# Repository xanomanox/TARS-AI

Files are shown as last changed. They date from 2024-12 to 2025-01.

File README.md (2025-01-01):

<h1 align="center">TARS-AI</h2>

<p align="center">
    <a href="https://discord.gg/uXkqkz3mJJ">
      
    </a>
    <a href="https://www.youtube.com/@TARS-AI.py.youtube">
        
    </a>
    <a href="https://www.instagram.com/tars.ai.py">
        
    </a>
    <a href="https://www.tiktok.com/@tars.ai.py">
        
    </a>
</p>

<p align="center"></p>

A recreation of the TARS robot from Interstellar, featuring AI capabilities and servo-driven movement. 

## Table of Contents
- [Hardware Requirements](#hardware-requirements)
- [Software Stack](#software-stack)
- [Build Modifications](#build-modifications)
- [License](#license)
- [Contributing](#contributing)
- [Additional Resources](#additional-resources)

## Hardware Requirements 

Everything here is **under development** and is subject to change.

| Category | Component | Description | Link |
|---|---|---|---|
| **Printing** | Bambu Labs Printer | Compatible models: P1S, A1, X1C | - |
| | TPU Filament (Bambu) | For all "Flexor" parts | [Buy](https://us.store.bambulab.com/products/tpu-for-ams) |
| | TPU Filament (Alternative) | Overture TPU filament | [Buy](https://www.amazon.com/Overture-Filament-Flexible-Consumables-Dimensional/dp/B07VDP2S3P/) |
| | PETG Filament | For all non-Flexor parts | [Buy](https://us.store.bambulab.com/products/petg-hf) |
| | PLA Filament | Optional - for rapid prototyping | - |
| **Core Components** | Raspberry Pi 5 | Main computing unit | [Buy](https://www.amazon.com/Raspberry-Pi-Quad-core-Cortex-A76-Processor/dp/B0CTQ3BQLS/) |
| | 3.5" LCD Display | Interface display | [Buy](https://www.amazon.com/OSOYOO-3-5inch-Display-Protective-Raspberry/dp/B09CD9W6NQ/) |
| | 16-Channel PWM Servo Driver | I2C Interface | [Buy](https://www.amazon.com/gp/product/B00EIB0U7A/) |
| | Buck Converter | Power management | [Buy](https://www.amazon.com/gp/product/B07SGJSLDL/) |
| **Servo Motors** | diymore MG996R | Digital servo motors (2x 90g micro servos per leg) | [Buy](https://www.amazon.com/diymore-6-Pack-MG996R-Digital-Helicopter/dp/B0CGRP59HJ/) |
| | MG996R 55g (Alternative) | Digital RC servo motors with high torque | - |
| **Drive Train** | Bearings | Motion support | [Buy](https://www.amazon.com/gp/product/B07FW26HD4/) |
| | Springs | Motion dampening | [Buy](https://www.amazon.com/gp/product/B076M6SFFP/) |
| | Metal Rods (Option 1) | Structural support | [Buy](https://www.amazon.com/gp/product/B01MAYQ12S/) |
| | Metal Rods (Option 2) | Alternative structural support | [Buy](https://www.amazon.com/gp/product/B0CTSX8SJS/) |
| | Linkage | Motion transfer | [Buy](https://www.amazon.com/gp/product/B0CRDRWYXW/) |
| | Servo Extension Wires | Connection cables | [Buy](https://www.amazon.com/OliYin-7-87in-Quadcopter-Extension-Futaba/dp/B0711TBZY2/) |
| **Audio System** | Raspberry Pi Microphone | Audio input | [Buy](https://www.amazon.com/gp/product/B086DRRP79/) |
| | Audio Amplifier | Sound processing | [Buy](https://www.amazon.com/dp/B0BTBS5NW2) |
| | Speaker | Audio output | [Buy](https://www.amazon.com/dp/B07GJ4GH67) |
| **Camera System** | Camera Module | Visual input | [Buy](https://a.co/d/50BbE8a) |
| | Camera Ribbon Cable | Camera connection | [Buy](https://www.amazon.com/Onyehn-Raspberry-Camera-Cable-Ribbon/dp/B07XZ5DX5H/) |
| **Fasteners** | M3 20mm Screws | Mounting (6x needed) | [Buy](https://www.amazon.com/gp/product/B0CR6DY4SS/) |
| | M3 14mm Screws | Mounting (40x needed) | [Buy](https://www.amazon.com/gp/product/B0D9GW9K4G/) |
| | M3 10mm Screws | Mounting (76x needed) | [Buy](https://www.amazon.com/gp/product/B0CR6G5XWC/) |
| | M3 Asstd Grub Screws | Mounting (6-8 needed) | [Buy](https://www.amazon.com/dp/B07N7C6HKP/) |

## Software Stack

See [`ENVSETUP.md`](./ENVSETUP.md) for instructions on setting up the software environment.

GPTARS Software Demo (https://www.youtube.com/watch?v=4YObs8BV3Mc)

- **LLM**: Choice of:
  - OpenAI (Recommended)
  - Oobabooga
  - Tabby ([tabbyAPI](https://github.com/theroyallab/tabbyAPI))
  - Ollama (Soon)
- **Text-to-Speech**: Choice of:
  - Azure TTS
  - Local (E-speak)
  - Local (Piper TTS with custom Voice model) (Recommended)
  - XTTSv2 with voice cloning ([xtts-api-server](https://github.com/daswer123/xtts-api-server))
- **Speech-to-Text**:
  - Vosk
  - Whisper
- **Vision Handling**:
  - Saleforce Blip
- **Tool Utilization**:
  - Custom Module Engine

## Build Modifications
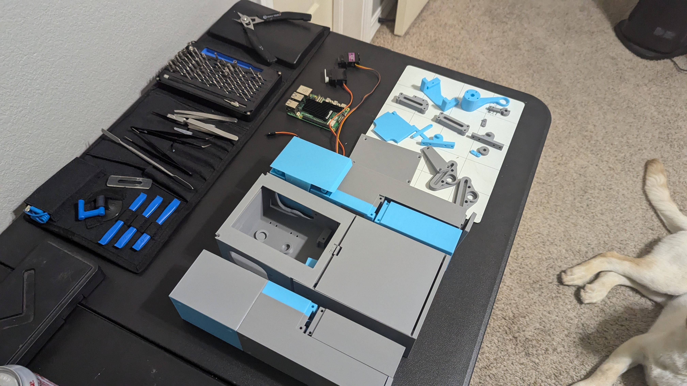
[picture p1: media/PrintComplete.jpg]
print

- Modified chassis bottom to accommodate SD card installation (See: "Chassis Bottom (Mod SD CARD).stl")

## License
[CC-BY-NU License](./LICENSE)

## Contributing
See [`CONTRIBUTING.md`](./CONTRIBUTING.md) for instructions on contributing to this project.

## Additional Resources
Inspirations + Credits to:
- [@charliediaz](https://www.hackster.io/charlesdiaz/how-to-build-your-own-replica-of-tars-from-interstellar-224833)
- [@gptars](https://www.youtube.com/@gptars)
- [@wizard.py](https://www.instagram.com/wizard.py/)
- [@poboisvert](https://github.com/poboisvert/GPTARS_Interstellar)

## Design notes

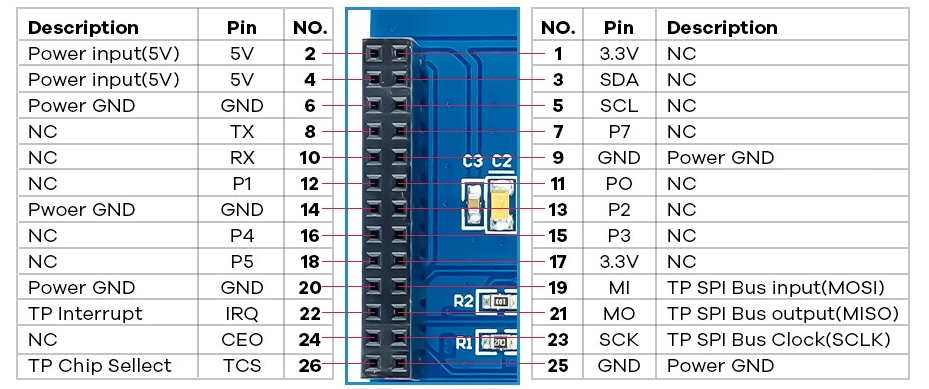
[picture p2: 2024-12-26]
Hardware/LCD PINOUT.png

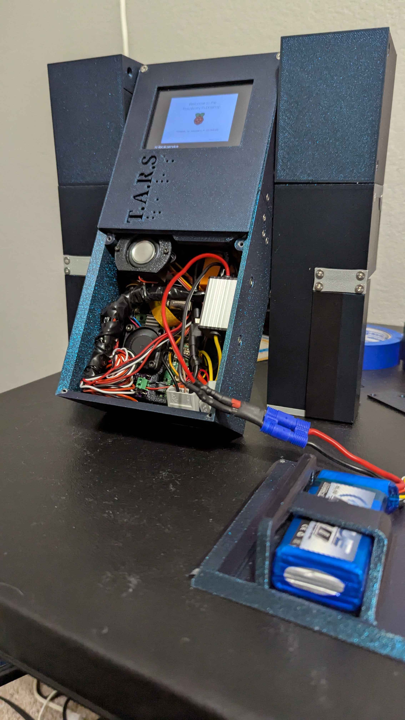
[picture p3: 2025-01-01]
media/preview.png

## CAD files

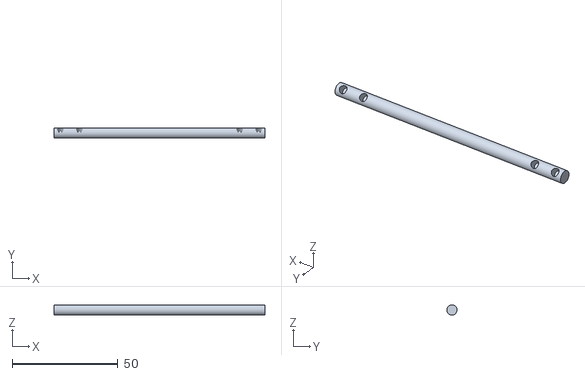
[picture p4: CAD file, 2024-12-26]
3d Printer Files/Main Axle.stl
100.0 x 4.80 x 4.80

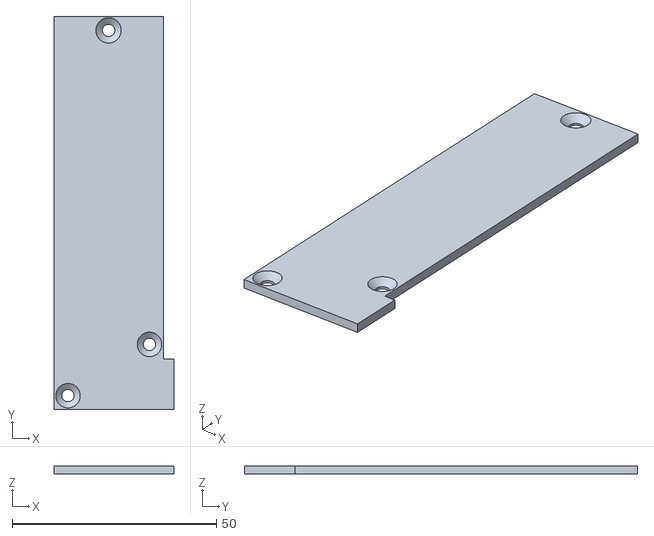
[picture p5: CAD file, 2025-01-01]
3d Printer Files/Arm Right Long Finger Lid countersunk.stl
29.4 x 96.3 x 2.00

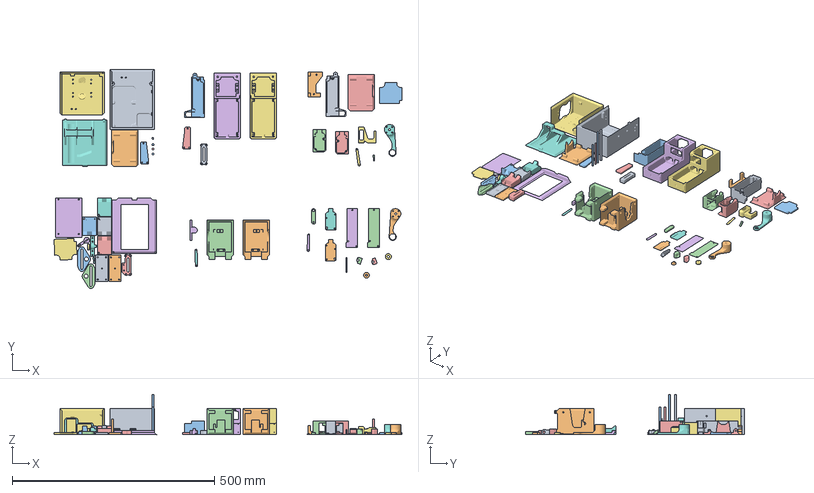
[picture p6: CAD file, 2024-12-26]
3d Printer Files/Other/GPTARs Files.3mf
859.8 x 541.4 x 100.0 mm
Main Axle.stl
Starboard Hull.stl
Lid B (1)(Mirror)(1).stl
Port Hull.stl
Port Component 233.stl
Starboard Suspension Mount.stl
Starboard Component 235.stl
Internal Hand 3 (1)(2)(2).stl
Main Arm (Mirror)_1.stl
Vertical Servo Clip (1).stl
Axle.stl
Forearm (1).stl
Forearm (1)(Mirror).stl
Port Component 234.stl
Screen Support.stl
Main Leg Mount (4).stl
Chassis (2).stl
Main Leg Mount (3).stl
Main ARM_1.stl
Lid Arm 2.stl
Servo Clip (Mirror).stl
Lid Arm 2(Mirror).stl
Chassis.stl
Lid Arm.stl
Sus Mount (1).stl
Lid Arm (Mirror).stl
Secondary Axle.stl
Pusher Rod.stl
Secondary Axle 2.stl
Internal Hand 3 (1)(2)(5).stl
TPU NewFlexor.stl
Lower Lid.stl
Conncting Arm.stl
Starboard Component 233.stl
Servi Clip.stl
Upper Strut Mount.stl
Upper Strut Mount 1.stl
Screen Lid.stl
Port NP - Mount Bearing.stl
Finger2.stl
Finger 2(Mirror).stl
Spacer.stl
Finger 1.stl
Internal Hand 1 (1)(2)(3).stl
Finger 1(Mirror).stl
Port Lid A.stl
Port Lid B.stl
Port Suspension Mount.stl
Foot Pad (1)(Mirror).stl
Port Foot Pad.stl
Starboard Spring Driver.stl
Port Spring Driver.stl
Sus Mount.stl
sk7_2 v1 (1).stl
Starboard NP - Mount Bearing.stl
Internal Hand 3 (1)(2).stl

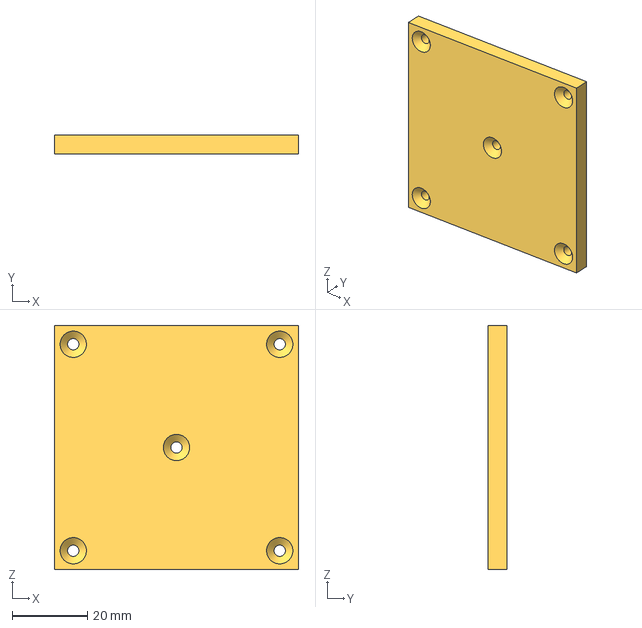
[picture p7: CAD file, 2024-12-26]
3d Printer Files/simplified_tars/footpad-simplified.3mf
65.0 x 5.00 x 65.0 mm

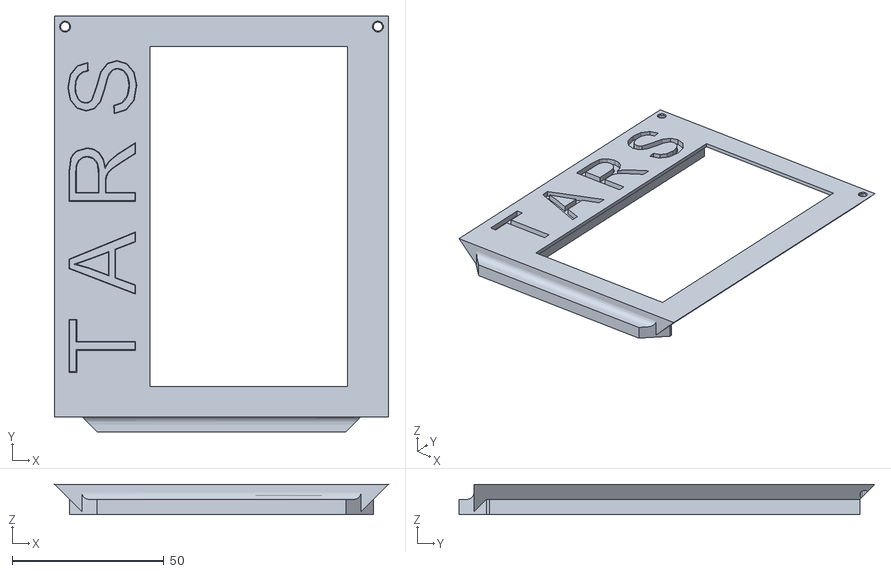
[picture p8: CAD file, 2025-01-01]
3d Printer Files/Chassis upper lid modded holes narrow 5in.stl
110.0 x 137.0 x 10.0

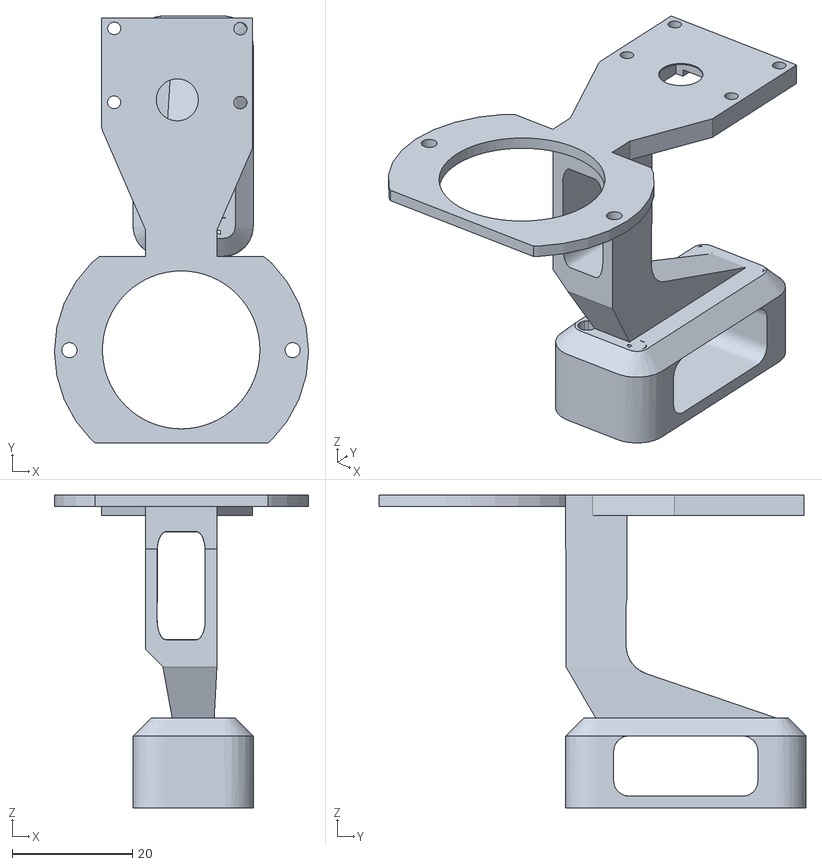
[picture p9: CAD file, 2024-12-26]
3d Printer Files/Other/RPI CAM and Speaker Mount.stl
42.3 x 71.1 x 52.1

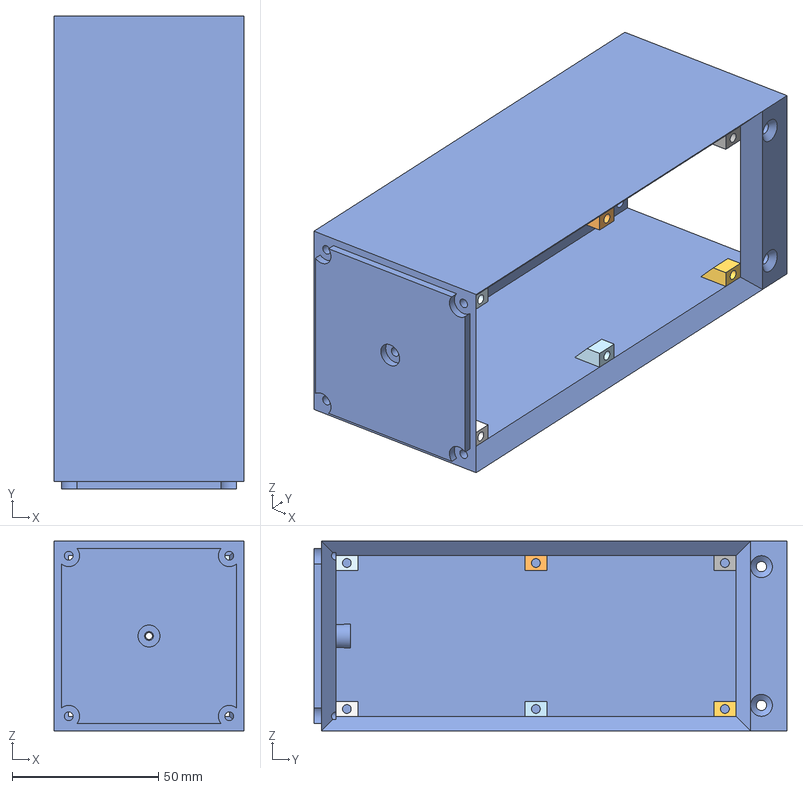
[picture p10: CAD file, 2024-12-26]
3d Printer Files/simplified_tars/leg - simplified.3mf
65.0 x 162.0 x 65.0 mm

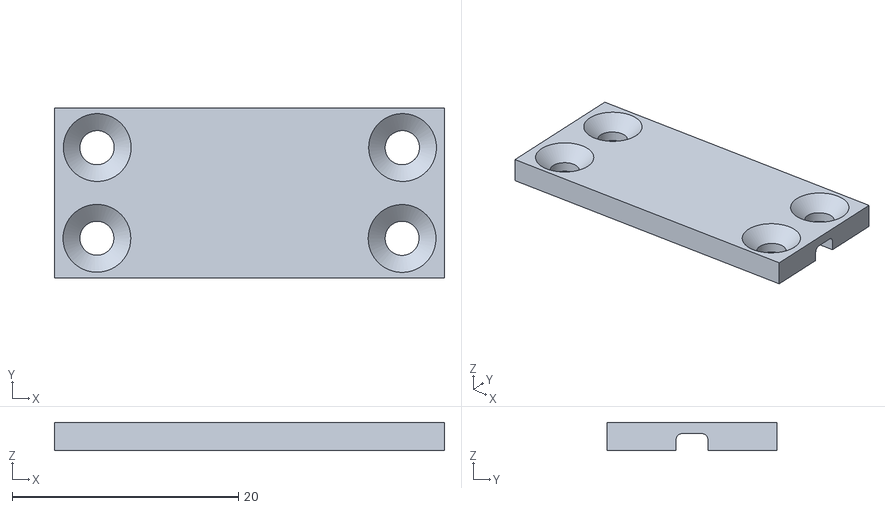
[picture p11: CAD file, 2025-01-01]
3d Printer Files/NewFlexor countersunk x2.stl
34.5 x 15.0 x 2.50

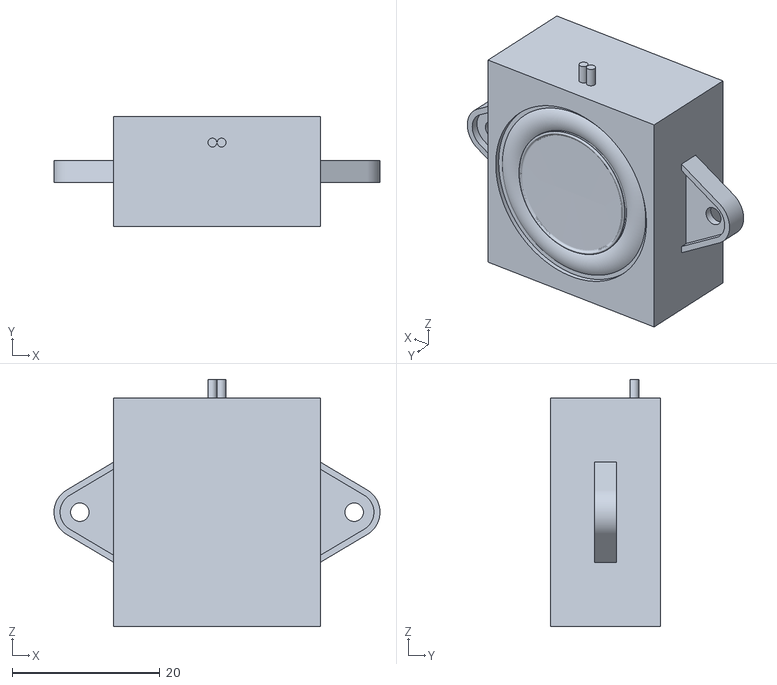
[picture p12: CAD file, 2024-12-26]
3d Printer Files/Other/Speaker.stl
44.2 x 14.9 x 33.5

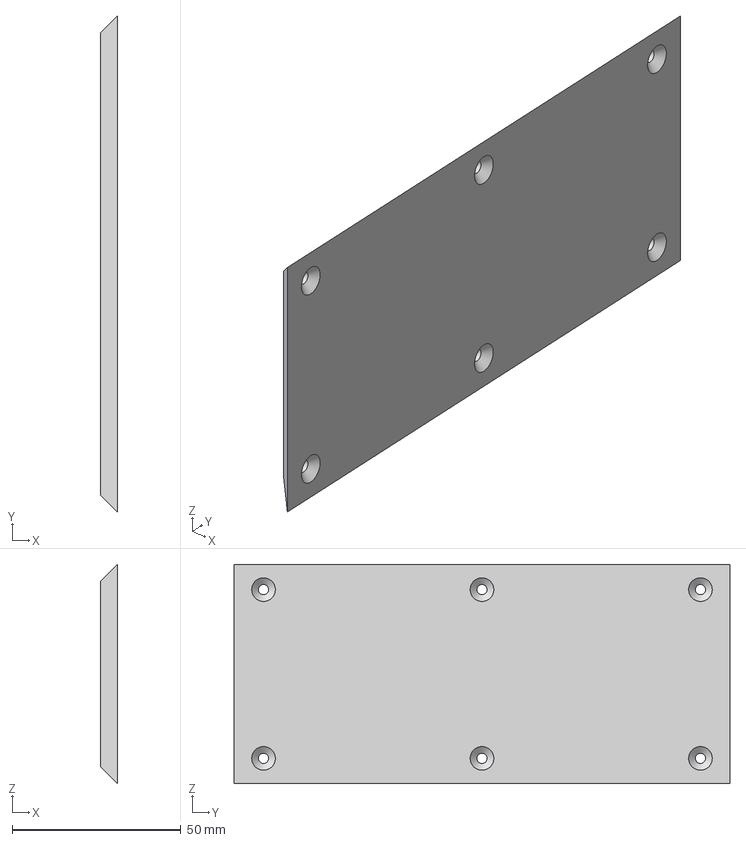
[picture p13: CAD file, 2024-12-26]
3d Printer Files/simplified_tars/leg_simplified-lid.3mf
5.00 x 147.0 x 65.0 mm

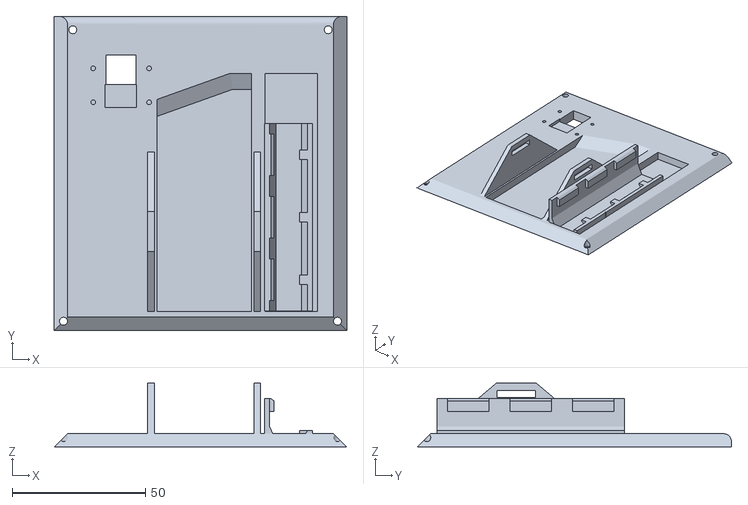
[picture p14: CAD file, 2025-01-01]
3d Printer Files/Chassis Lower Lid Pi camv3 and termblock (v9).stl
110.0 x 118.0 x 24.0

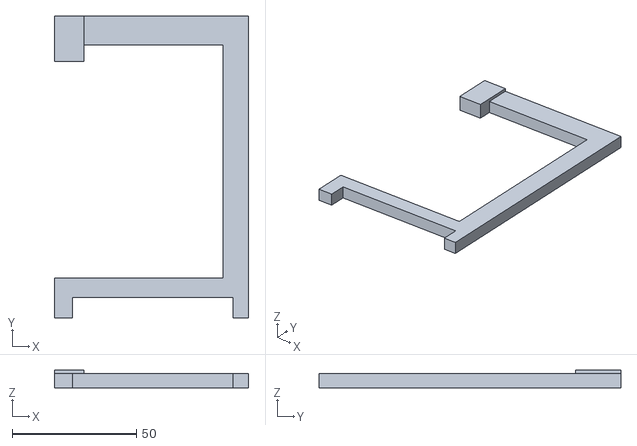
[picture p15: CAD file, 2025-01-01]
3d Printer Files/5in display spacer.stl
78.2 x 121.6 x 7.15

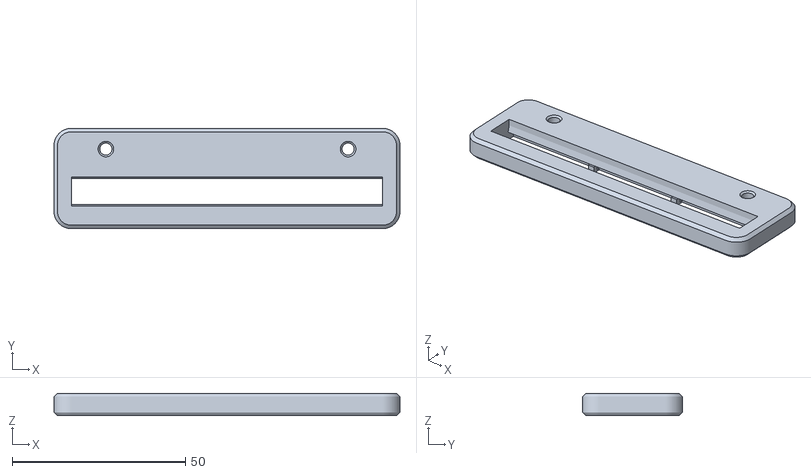
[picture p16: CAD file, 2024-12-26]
3d Printer Files/Other/PCT Linear Base Mount.stl
100.0 x 29.0 x 6.50

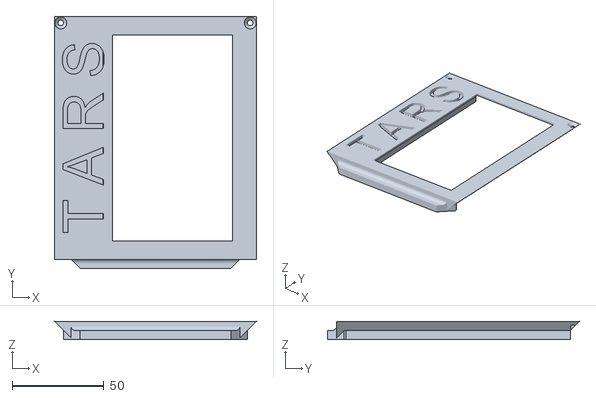
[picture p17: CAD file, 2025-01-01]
3d Printer Files/Chassis Upper Lid v9 5in narrow.stl
110.0 x 137.0 x 10.0

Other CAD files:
3d Printer Files/Chassis Lower Lid MOD PCT (mirror) makes space for GPIO.stl
3d Printer Files/Other/battery.stl
3d Printer Files/Chassis Upper Lid (v9) Speaker and Cam Mod.stl
3d Printer Files/Other/buck convertor.stl
3d Printer Files/Arm Chasis Lid x2.stl
3d Printer Files/Arm Left (Top Chassis).stl
3d Printer Files/Arm Left 1 Finger.stl
3d Printer Files/Arm Left 2 Finger.stl
3d Printer Files/Arm Left Footpad.stl
3d Printer Files/Arm Left Insert.stl
3d Printer Files/Arm Left Long Finger Lid.stl
3d Printer Files/Arm Left Long Finger.stl
3d Printer Files/Arm Left Lower Chasis.stl
3d Printer Files/Arm Left Lower Chassis MOD 3mm servoscrews.stl
3d Printer Files/Arm Left Mount.stl
3d Printer Files/Arm Left NP - Mount Bearing.stl
3d Printer Files/Arm Left Small Finger Lid.stl
3d Printer Files/Arm Left Spring Driver.stl
3d Printer Files/Arm Left Top Lid.stl
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

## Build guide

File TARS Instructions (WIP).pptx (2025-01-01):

## TARS Instructions

Screws Needed:
6 M20
40 M14
76 M10

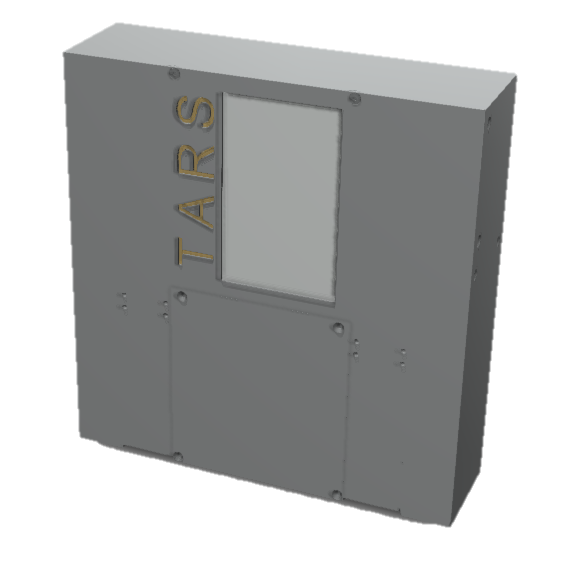
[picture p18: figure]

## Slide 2

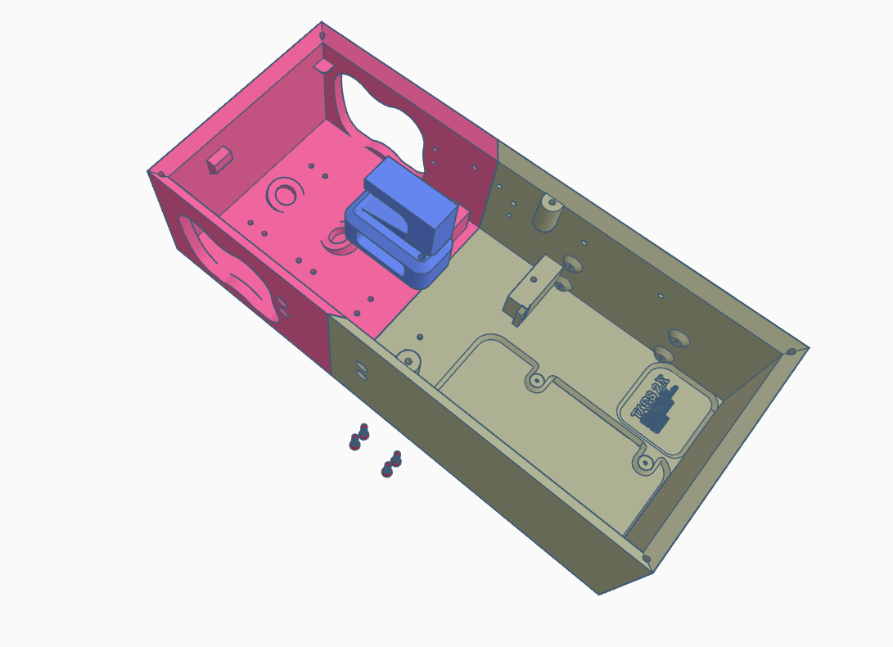
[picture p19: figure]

Chassis Upper (v9)

Chassis Lower (v9)

Chassis Connector Screen Support

M3 20MM x4

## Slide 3

x2

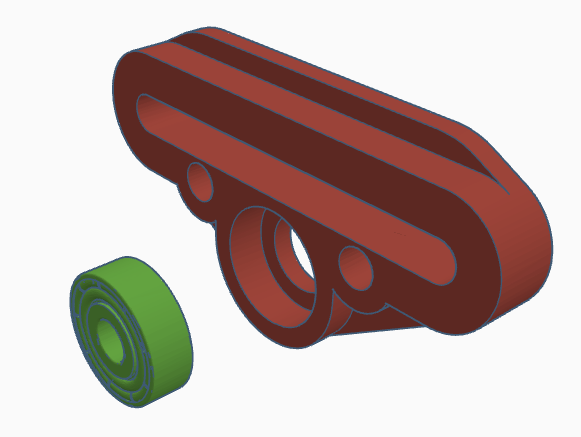
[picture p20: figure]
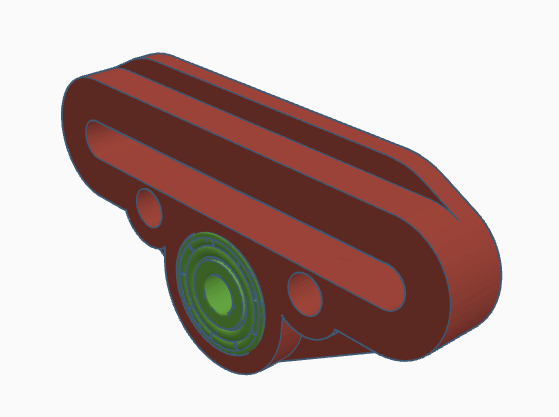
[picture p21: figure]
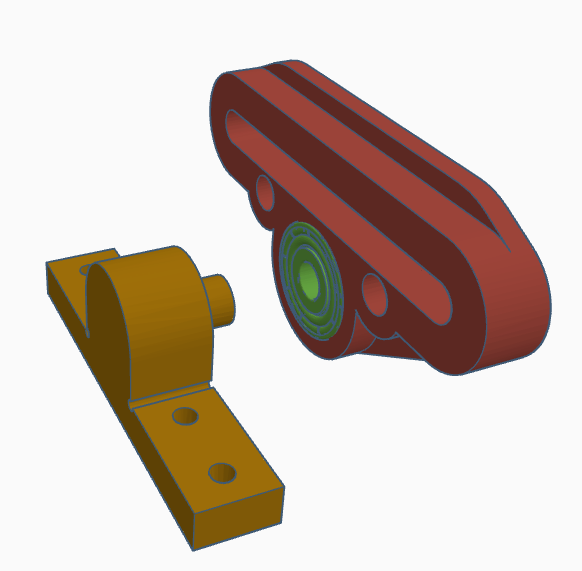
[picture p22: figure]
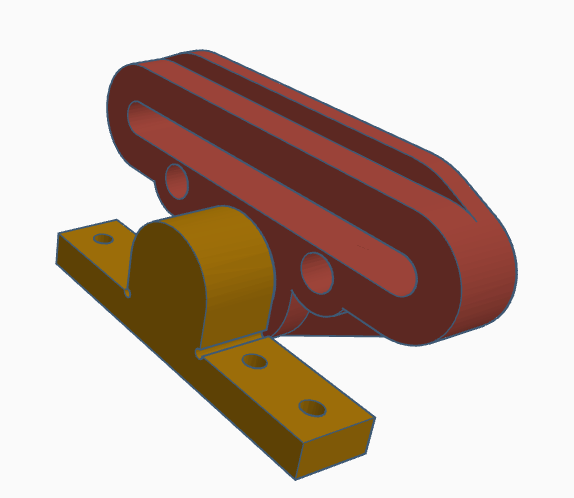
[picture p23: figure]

Arm Spring Divider
(left and Right)

608 Bearing
(metal or Printed)

Arm Suspension Mount

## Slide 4

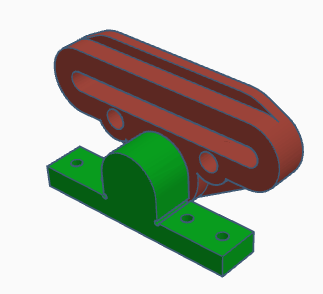
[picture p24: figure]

Assembly from previous step x2

Arm Suspension Mount x8

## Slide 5

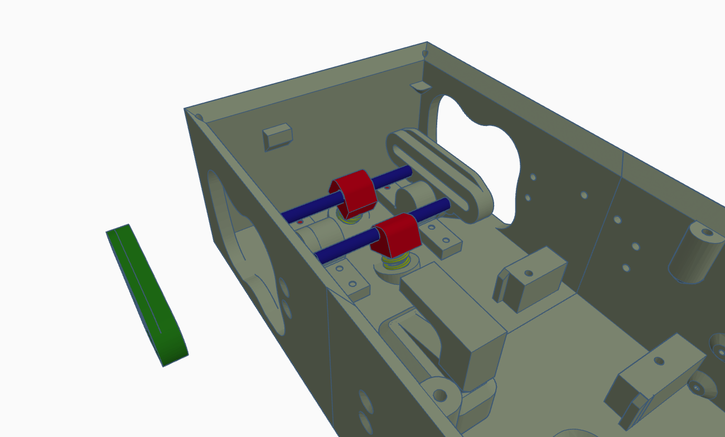
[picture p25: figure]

Secondary Axle x2

Spring x2

Upper Strut Mount x2

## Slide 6

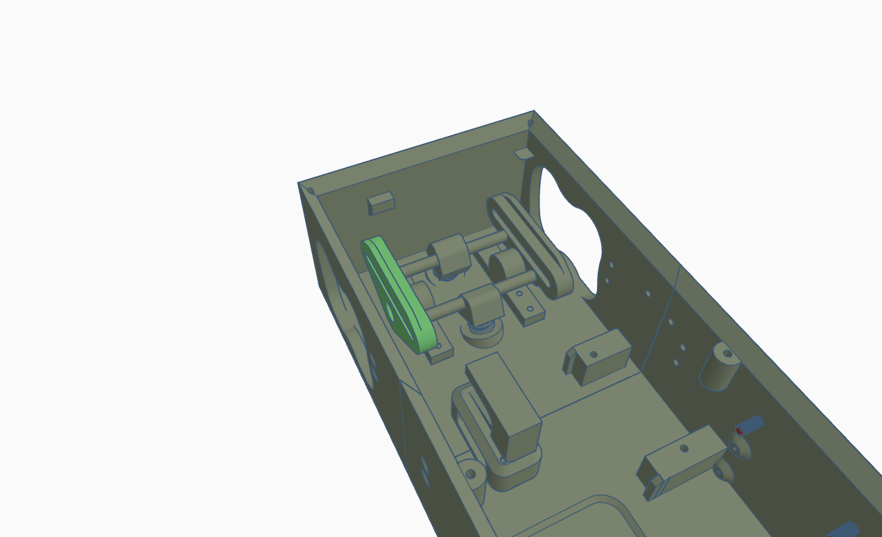
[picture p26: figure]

Reinstall

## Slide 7

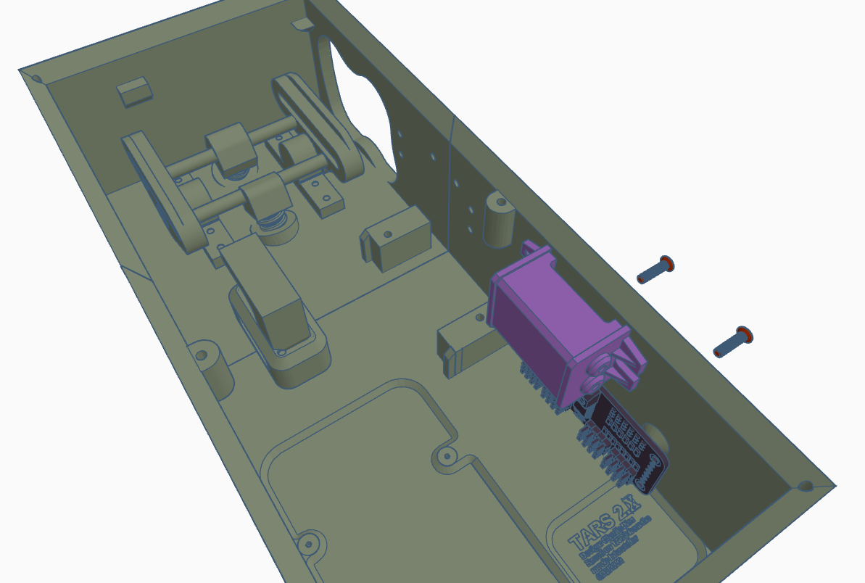
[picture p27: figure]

Secure the 12 ch PWM board to the wall with 4 M2*4 screws (use a flat tip by hand)
Connect the 6v out wires to the
Secure the 12v to 6v Buck convertor with 2 M3*10 screws

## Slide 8

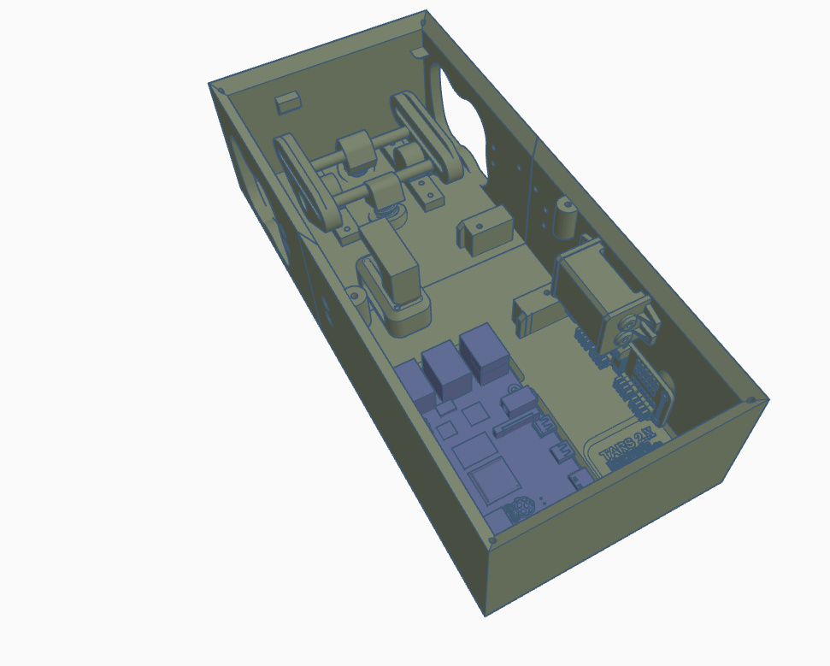
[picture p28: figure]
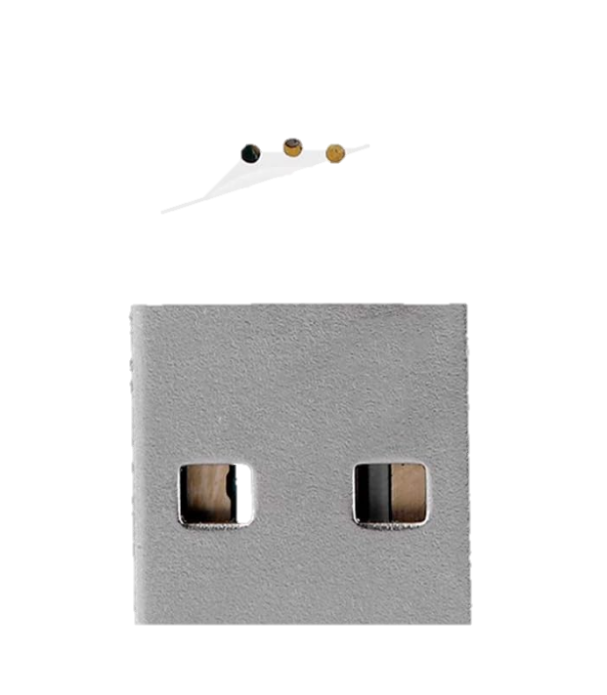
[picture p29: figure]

Insert the USB MIC into the RPI
(Not shown here)
Insert the RPI and secure with 4 M2*4 screws. DO NOT OVER TIGHTEN OR USE LONGER SCREWS

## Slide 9

“5 Pack ShareGoo 25T Aluminum Servo Horns M3 Threads Metal Steering Arm for RC Car Truck Buggy Airplane-Black”

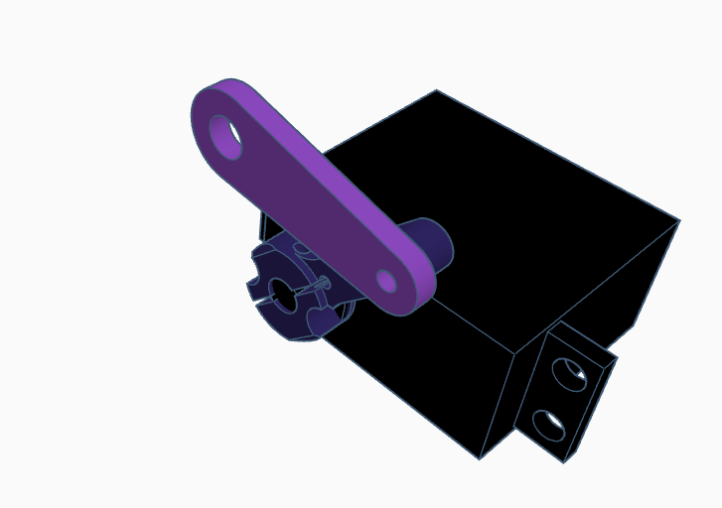
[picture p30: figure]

Attach a METAL !!! (unable to print it WILL strip) 25T Aluminum Servo Horn with M3 Threads to the servo using supplied hardware.
Attach upper connecting rod arm with M3*12 screw like arrow shown

## IMPORTANT STEP!!!!!!!

Connect Servos to the Servo Controller:
- Attach the center servo to the first set of pins on the servo controller (Pin 0).
- Connect the robot's left (port) arm to the next set of pins (Pin 1).
- Connect the robot's right (starboard) arm to the following set of pins (Pin 2).
Connect the PWM Servo Controller to the Raspberry Pi:
- Use the servotester.py script to determine the minimum and maximum PWM values the servo can operate within.
- Calculate the dead center value (midpoint) between the minimum and maximum PWM values.
- Manually attach the arms at the midpoint position to ensure proper alignment.
Update the Configuration File:
- Add the determined center PWM value as neutral to the config.ini file. Add 50 to neutral for up and subtract 50 for down limits.
Center the Arms Mechanically:
- Using the servo test tool, set each arm's servo channel to a midpoint value, such as 350 (between the typical range of 100-600).
- Detach the arms, reposition them to align mechanically with the center position, and then reattach them.
- This ensures the arms are mechanically centered at the specified midpoint value (e.g., 350). For example if you set 350 they should be vertical and perfectly straight.
Calibrate the Center Servo:
- Set the center servo to its lowest position (e.g., 88) using the servo test tool.
- Reposition and reattach the center servo to align with the lowest point.
- Define this position (e.g., 88) as UPHEIGHT in the config.ini file.

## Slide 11

x2

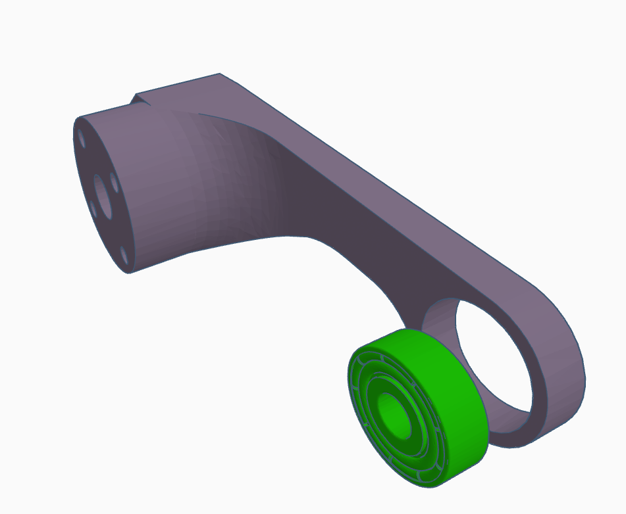
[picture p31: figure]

Press in the 608 bearing (metal or printed) in the Arm Left / Right Mount

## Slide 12

x2

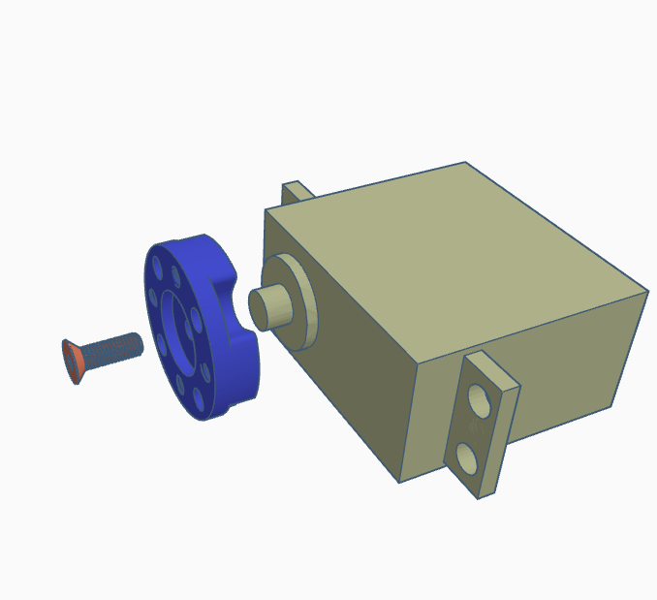
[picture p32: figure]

Connect servo to RPI first, the PORT and STARBOARD servos should go in pin 1 and 2 (the first pin is 0).

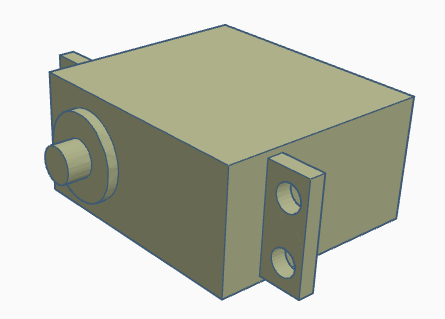
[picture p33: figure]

Servo

Arm Upper Servo Horn

Servo Horn Screw

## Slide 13

x2

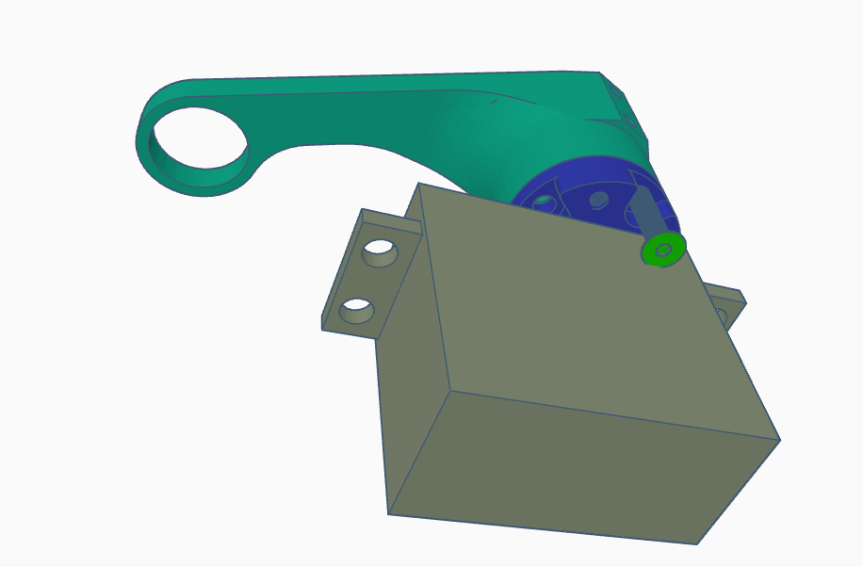
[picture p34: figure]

Servo

Arm Upper Servo Horn

M3 14MM x4

*Rotate the servo to align the bolts

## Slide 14

x2

Servo

Arm Upper Servo Horn

M3 14MM x4

*Rotate the servo to align the bolts

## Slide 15

Insert secondary Axle main lifting rod into center servo.

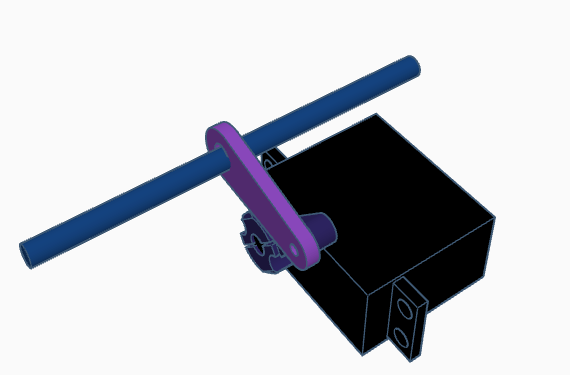
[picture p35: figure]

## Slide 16

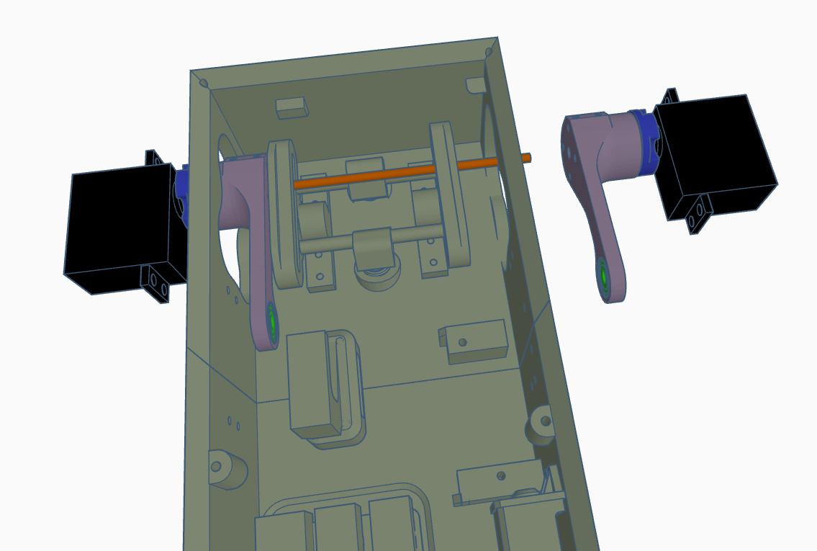
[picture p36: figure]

Slide the Left arm mount in
Slide in upper rod and screw into place.
Repeat process on
right side

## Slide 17

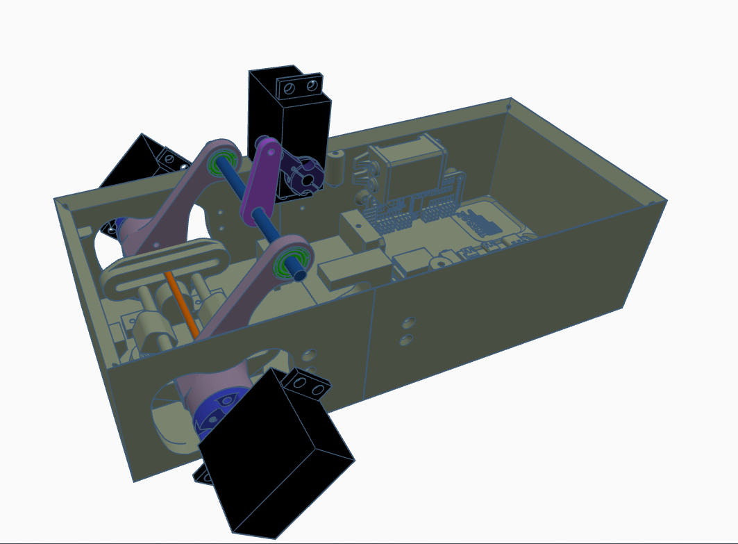
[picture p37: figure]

Rotate main arms and slide in center servo rod assembly.

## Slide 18

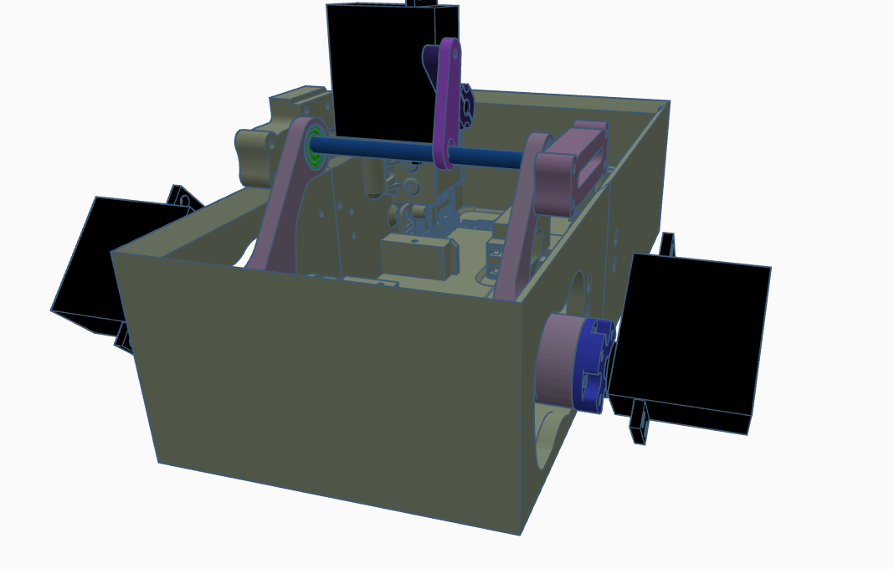
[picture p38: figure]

Slide on main body mounts

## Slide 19

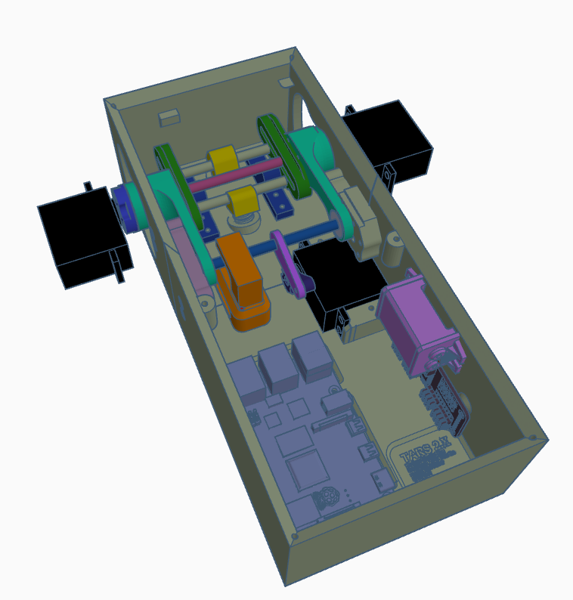
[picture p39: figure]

Rotate entire assembly into place
Secure sides with m4*10 screws

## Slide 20

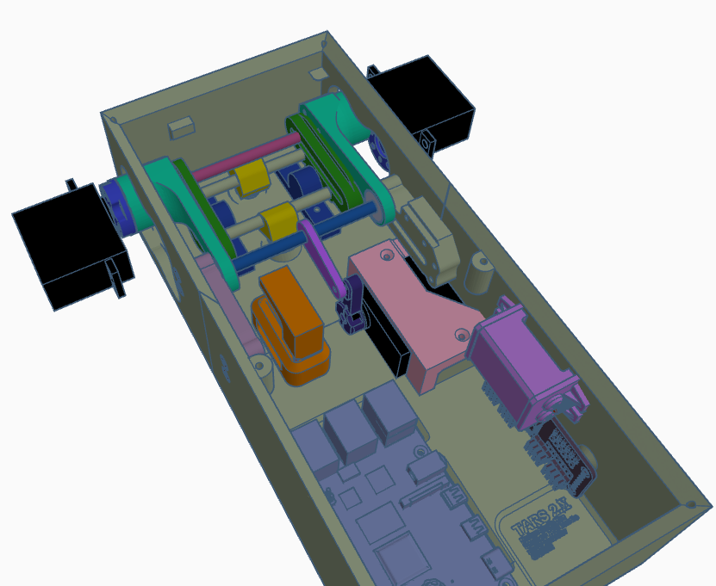
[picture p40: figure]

Slide Arm assembly up and attach
Center servo bracket.

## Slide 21

x2

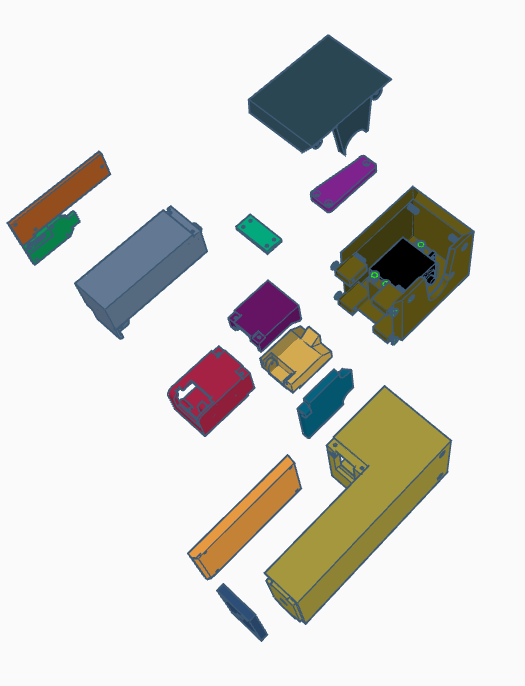
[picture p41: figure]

Each arm is assembly like the picture

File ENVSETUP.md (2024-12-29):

# ENVSETUP.md

## Minimum Hardware Prerequisites

1. **Raspberry Pi**: For obvious reasons.
2. **USB Microphone**: For user input.
3. **Speaker**: For TARS output.

---

## Environment Setup Guide (IN DEVELOPMENT)

### 1. Set Up the TARS-AI Repository on Raspberry Pi

#### A. Clone the Repository
1. Open a terminal on your Raspberry Pi.
2. Clone the **TARS-AI** repository:
   ```bash
   git clone https://github.com/pyrater/TARS-AI.git
   ```
3. Navigate to the cloned directory:
   ```bash
   cd TARS-AI
   ```

#### B. Install System-Level Dependencies
These dependencies are required for various operations, including Selenium-based automation, audio processing, and format handling.

1. **Update Your System**:
   Ensure your package lists and installed software are up to date:
   ```bash
   sudo apt update
   sudo apt upgrade -y
   ```

2. **Install Chromium**:
   Chromium is the browser required for Selenium-based web automation:
   ```bash
   sudo apt install -y chromium-browser
   ```

3. **Install Chromedriver for Selenium**:
   Chromedriver allows Selenium to control Chromium:
   ```bash
   sudo apt install -y chromium-chromedriver
   ```

4. **Install SoX and Format Support Libraries**:
   SoX is a command-line tool for processing audio files. 
   ```bash
   sudo apt install -y sox libsox-fmt-all
   ```

5. **Install PortAudio Development Libraries**:
   PortAudio is a cross-platform audio input/output library.
   ```bash
   sudo apt install -y portaudio19-dev
   ```

6. **Verify Installations**:
   Confirm that the installed packages are functioning:
   - Check Chromium version:
     ```bash
     chromium-browser --version
     ```
   - Check Chromedriver version:
     ```bash
     chromedriver --version
     ```
   - Check SoX version:
     ```bash
     sox --version
     ```

#### C. Set Up the Python Environment

1. Create a virtual environment:
   ```bash
   python3 -m venv venv
   ```
2. Activate the virtual environment:
   ```bash
   source venv/bin/activate
   ```
3. Install the required dependencies under `src/`:
   ```bash
   pip install -r requirements.txt
   ```

#### D. Connect Hardware

1. Connect your **microphone** to the Raspberry Pi via USB.
2. Connect your **speaker** to the Raspberry Pi using the audio output or Bluetooth.

#### E. Set the API Key in a `.env` File (Recommended for Secure Key Management)

**Create** a `.env` file at the root of your repository based on the pre-existing .env.template file to store your API keys for your LLM and TTS service.

**`.env` Template**:
   Add the following lines to your `.env` file. Replace `your-actual-api-key` with your actual API key for the desired service:
   ```env
   # LLM
   OPENAI_API_KEY="your-actual-openai-api-key"
   OOBA_API_KEY="your-actual-ooba-api-key"
   TABBY_API_KEY="your-actual-tabby-api-key"

   # TTS
   AZURE_API_KEY="your-actual-azure-api-key"
   ```
   - Set up an OpenAI API Key (very small cost) - [OpenAI API Key](https://www.youtube.com/watch?v=OB99E7Y1cMA)
   - Set up an Azure Speech API Key (FREE) - [Azure Speech API Key](https://www.youtube.com/watch?v=e4_AytZ264Q)
      - Make sure to create a Free Azure account [Free Azure Signup](https://azure.microsoft.com/en-us/pricing/purchase-options/azure-account?icid=azurefreeaccount)
      - Follow all the steps in the video up to `Install Azure speech Python package`.

#### F. Set the config.ini Parameters 

1. **Create** a `config.ini` file in the `src/` folder based on the pre-existing config.ini.template file.

2. Locate the `[LLM]` section and update the parameters (for OpenAI):
   ```ini
   [LLM] # Large Language Model configuration (ooba/OAI or tabby)
   llm_backend = openai
   # Set this to `openai` if using OpenAI models.
   base_url = https://api.openai.com
   # The URL for the OpenAI API.
   openai_model = gpt-4o-mini
   # Specify the OpenAI model to use (e.g., gpt-4o-mini or another supported model).
   ```

3. Locate the `[TTS]` section and update the parameters:
   ```ini
   [TTS] # Text-to-Speech configuration 
   ttsoption = azure
   # TTS backend option: [azure, local, xttsv2, TARS]
   azure_region = eastus
   # Azure region for Azure TTS (e.g., eastus)
   ...
   tts_voice = en-US-Steffan:DragonHDLatestNeural
   # Name of the cloned voice to use (e.g., TARS2)
   ```
- `tts_voice`: You can find other voices available with Azure [here](https://learn.microsoft.com/en-us/azure/ai-services/speech-service/language-support?tabs=tts).
   - If en-US-Steffan:DragonHDLatestNeural gives you an error, try en-US-SteffanNeural.

#### G. Run the Program
1. Navigate to the `src/` folder within the repository:
   ```bash
   cd src/
   ```
2. Start the application:
   ```bash
   python app.py
   ```
3. The program should now be running and ready to interact using your microphone and speaker.

## (OPTIONAL) Set up XTTS Server

### 1. Prepare Your PC with NVIDIA GPU
The TTS server must run on your GPU-enabled PC due to its computational requirements.

1. Ensure **Python 3.9-3.12** is installed on your PC.
2. Install **CUDA** and **cuDNN** compatible with your NVIDIA GPU - [CUDA Installation](https://www.youtube.com/watch?v=krAUwYslS8E)
3. Install **PyTorch** compatible with your CUDA and cuDNN versions - [PyTorch Installation](https://pytorch.org/get-started/locally/)

---

### 2. Set Up XTTS API Server

#### A. Install XTTS API Server
Run the following command on your GPU-enabled PC to clone the [XTTS API Server repository](https://github.com/daswer123/xtts-api-server):

```bash
git clone https://github.com/daswer123/xtts-api-server.git
```

Follow the installation guide for your operating system:
- **Windows**:
  1. Create and activate a virtual environment:
     ```bash
     python -m venv venv
     venv\Scripts\activate
     ```
  2. Install xtts-api-server:
     ```bash
     pip install xtts-api-server
     ```

For more details, refer to the official [XTTS API Server Installation Guide](https://github.com/daswer123/xtts-api-server/tree/main).

#### B. Add the TARS.wav Speaker File
1. Download the `TARS-short.wav` and `TARS-long.wav` files from the `TARS-AI` repository under `src/tts/wakewords
/VoiceClones`. These will be the different voices you can use for TARS.
2. Place it in the `speakers/` directory within the XTTS project folder. If the directory does not exist, create it.

#### C. Start the XTTS API Server
1. Open a terminal in the `xtts-api-server` project directory.
2. Activate your virtual environment if not already active:
3. Start the XTTS API Server:
   ```bash
   python -m xtts_api_server --listen --port 8020
   ```
4. Once the server is running, open a browser and navigate to:
   ```
   http://localhost:8020/docs
   ```
5. This will open the API's Swagger documentation interface, which you can use to test the server and its endpoints.

#### D. Verify the Server
1. Locate the **GET /speakers** endpoint in the API documentation.
2. Click **"Try it out"** and then **"Execute"** to test the endpoint.
3. Ensure the response includes the `TARS-Short` and `TARS-Long` speaker files, with entries similar to:
   ```json
   [
     {
       "name": "TARS-Long",
       "voice_id": "TARS-Long",
       "preview_url": "http://localhost:8020/sample/TARS-Long.wav"
     },
     {
       "name": "TARS-Short",
       "voice_id": "TARS-Short",
       "preview_url": "http://localhost:8020/sample/TARS-Short.wav"
     }
   ]
   ```
4. Locate the **POST /tts_to_audio** endpoint in the API documentation.
5. Click **"Try it out"** and input the following JSON in the **Request Body**:
   ```json
   {
       "text": "Hello, this is TARS speaking.",
       "speaker_wav": "TARS-Short",
       "language": "en"
   }
   ```
6. Click **"Execute"** to send the request.
7. Check the response for a generated audio file. You should see a download field where you can download and listen to the audio output.

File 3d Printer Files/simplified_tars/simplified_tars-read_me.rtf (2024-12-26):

These are fully redesigned by Michael Proctor (Manthis in Discord). I plan to slowly redesign the entire bot so future edits are easier to make (Editing STEP files can be a pain…).

Everything will be in a public Onshape project so feel free to make a copy of it and make your own edits.
I am a noob at design, so feel free to DM me on Discord any feedback you have.

Onshape Project: https://cad.onshape.com/documents/3fc66bce504b7e19d90aa795/w/4c55da55e44503ca82605304/e/a162dff2fca3f073a37a6638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

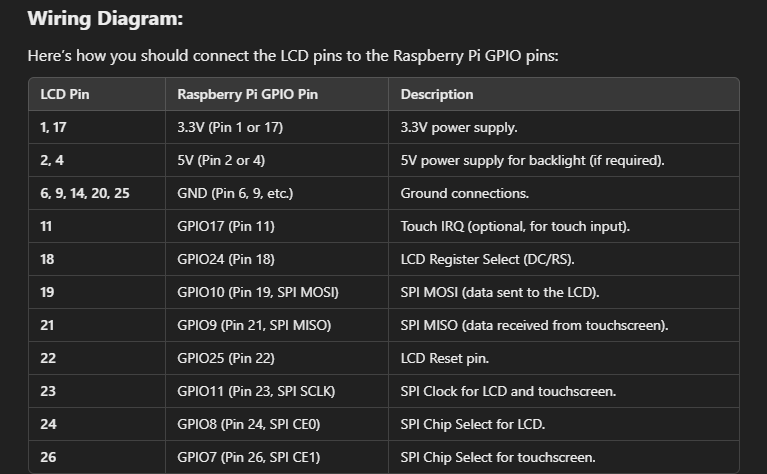
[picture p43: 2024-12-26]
Hardware/GPIO Wiring.png

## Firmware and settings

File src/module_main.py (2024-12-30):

"""
module_main.py

Core logic module for the TARS-AI application.

Integrates modules and manages key functionalities, including:
- Text-to-Speech (TTS) playback and configuration
- Interaction with Large Language Model (LLM) backends
- Prompt building and AI response processing
- Wake word handling and user interaction workflows
- Emotion detection and system threading
"""
# === Standard Libraries ===
import os
import threading
import json
import requests
import re
from datetime import datetime
import concurrent.futures

# === Custom Modules ===
from module_config import load_config
from module_btcontroller import start_controls
from module_engine import check_for_module
from module_tts import generate_tts_audio
from module_vision import get_image_caption_from_base64
from module_stt import STTManager

# === Constants and Globals ===
character_manager = None
memory_manager = None
stt_manager = None

CONFIG = load_config()

# Global Variables (if needed)
stop_event = threading.Event()
executor = concurrent.futures.ProcessPoolExecutor(max_workers=4)

# === Threads ===
def start_bt_controller_thread():
    """
    Wrapper to start the BT Controller functionality in a thread.
    """
    try:
        print(f"[{datetime.now().strftime('%Y-%m-%d %H:%M:%S')}] LOAD: Starting BT Controller thread...")
        while not stop_event.is_set():
            start_controls()
    except Exception as e:
        print(f"[{datetime.now().strftime('%Y-%m-%d %H:%M:%S')}] ERROR: Error in BT Controller thread: {e}")

# === Core Functions ===
def extract_text(json_response, picture):
    """
    Extracts text from the JSON response. Handles OpenAI's chat.completion and other structures.

    Parameters:
    - json_response (dict): The JSON response from the LLM backend.
    - picture (bool): Whether the response contains a picture or not.

    Returns:
    - str: The extracted text content from the response.
    """
    global character_manager
    
    try:
        # Determine the correct field for text extraction based on response structure
        if 'choices' in json_response:
            if CONFIG['LLM']['llm_backend'] == "openai":
                # For OpenAI's chat.completion API
                text_content = json_response['choices'][0]['message']['content']
                return text_content
            elif CONFIG['LLM']['llm_backend'] == "ooba" or CONFIG['LLM']['llm_backend'] == "tabby":
                # For other backends like Ooba or Tabby
                text_content = json_response['choices'][0]['text']
        else:
            raise KeyError("Invalid response format: 'choices' key not found.")

        # Clean up the text
        cleaned_text = re.sub(r"\s{2,}", " ", text_content.strip())  # Collapse multiple spaces
        cleaned_text = re.sub(r"<\|.*?\|>", "", cleaned_text, flags=re.DOTALL)  # Remove <|...|> tags
        
        if not picture:
            # Additional cleanup for non-picture responses
            cleaned_text = re.sub(rf"{re.escape(character_manager.char_name)}:\s*", "", cleaned_text)  # Remove character name prefix
            cleaned_text = re.sub(r"\n\s*\n", "\n", cleaned_text).strip()  # Remove empty lines

        return cleaned_text

    except (KeyError, IndexError, TypeError) as error:
        return f"Text content could not be found. Error: {str(error)}"

def set_emotion(text_to_read):
    """
    Function to set the emotion of the character based on the text generated by the AI.

    Parameters:
    - text_to_read (str): The text generated by the AI.
    """
    from transformers import pipeline
    global memory_manager
    
    sizecheck = memory_manager.token_count(text_to_read)
    if 'length' in sizecheck:
        value_to_convert = sizecheck['length']
    
    if isinstance(value_to_convert, (int, float)):
        if value_to_convert <= 511:
            classifier = pipeline(task="text-classification", model="SamLowe/roberta-base-go_emotions", top_k=None)
            model_outputs = classifier(text_to_read)
            emotion = max(model_outputs[0], key=lambda x: x['score'])['label']
            
            print(f"[{datetime.now().strftime('%Y-%m-%d %H:%M:%S')}] Emotion {emotion}")

def llm_process(userinput, botresponse):
    """
    Process the user input and bot response for various tasks.

    Parameters:
    - userinput (str): The user input text.
    - botresponse (str): The bot response text.

    Returns:
    - str: The processed bot response
    """
    global memory_manager

    threading.Thread(target=memory_manager.write_longterm_memory, args=(userinput, botresponse)).start()
    if CONFIG['EMOTION']['enabled'] == True: #set emotion
        threading.Thread(target=set_emotion, args=(botresponse,)).start()
    return botresponse

def build_prompt(user_prompt):
    """
    Build the prompt structure for the Large Language Model (LLM) backend.

    Parameters:
    - user_prompt (str): The user's input prompt.

    Returns:
    - str: The formatted prompt for the LLM backend.
    """
    global character_manager, memory_manager
    
    now = datetime.now() # Current date and time
    date = now.strftime("%m/%d/%Y")
    time = now.strftime("%H:%M:%S")

    # Handle toggling voice-only mode
    if "voice only mode on" in user_prompt:
        character_manager.voice_only = True
    elif "voice only mode off" in user_prompt:
        character_manager.voice_only = False

    module_engine = check_for_module(user_prompt)

    if module_engine == "Mute":
        #somehow needs to go back to listen for wake word
        return

    if module_engine != "No_Tool":
        #if "*User is leaving the chat politely*" in module_engine:
            #stop_idle() #StopAFK mssages

        if "Sends a picture***" in module_engine:
            sdpicture = module_engine.split('***', 1)[-1]
            #module_engine = f"*Sends a picture*. You will inform user that this is the image as requested, do not describe the image."
            
            pattern = r'data:image\/[a-zA-Z]+;base64,([^"]+)'
            match = re.search(pattern, sdpicture)
            if match:
                base64_data = match.group(1)
                module_engine = f"*Sends a picture of: {get_image_caption_from_base64(base64_data)}*"
            else:
                module_engine = f"*Cannot send a picture something went wrong, inform user*"
 
    # Build basic prompt structure
    dtg = f"Current Date: {date}\nCurrent Time: {time}\n"
    past = memory_manager.get_longterm_memory(user_prompt) # Get past memories
    # Correct the order and logic of replacements clean up memories and past json crap
    past = past.replace("\\\\", "\\")  # Reduce double backslashes to single
    past = past.replace("\\n", "\n")   # Replace escaped newline characters with actual newlines
    past = past.replace("\\'", "'")    # Replace escaped single quotes with actual single quotes
    past = past.replace("\'", "'")    # Replace escaped single quotes with actual single quotes

    history = ""
    userInput = user_prompt  # Simulating user input to avoid hanging

    if module_engine != "No_Tool":
        module_engine = module_engine + "\n"
    else:
        module_engine = ""

    promptsize = (
        f"System: {CONFIG['LLM']['systemprompt']}\n\n"
        f"### Instruction: {CONFIG['LLM']['instructionprompt']}\n"
        f"{dtg}\n"
        f"User is: {CONFIG['CHAR']['user_details']}\n\n"
        f"{character_manager.character_card}\n"
        f"Past Memories which may be helpful to answer {character_manager.char_name}: {past}\n\n"
        f"{history}\n"
        #f"{module_engine}"
        f"Respond to {CONFIG['CHAR']['user_name']}'s message of: {userInput}\n"
        f"{module_engine}"
        f"### Response: {character_manager.char_name}: "
    )
    # Calc how much space is avail for chat history
    remaining = memory_manager.token_count(promptsize).get('length', 0)
    memallocation = int(CONFIG['LLM']['contextsize'] - remaining)
    history = memory_manager.get_shortterm_memories_tokenlimit(memallocation)

    prompt = (
        f"System: {CONFIG['LLM']['systemprompt']}\n\n"
        f"### Instruction: {CONFIG['LLM']['instructionprompt']}\n"
        f"{dtg}\n"
        f"User is: {CONFIG['CHAR']['user_details']}\n\n"
        f"{character_manager.character_card}\n"
        f"Past Memories which may be helpfull to answer {character_manager.char_name}: {past}\n\n"
        f"{history}\n"
        f"Respond to {CONFIG['CHAR']['user_name']}'s message of: {userInput}\n"
        f"{module_engine}"
        f"### Response: {character_manager.char_name}: "
    )
    prompt = prompt.replace("{user}", CONFIG['CHAR']['user_name']) 
    prompt = prompt.replace("{char}", CONFIG['CHAR']['user_name'])
    prompt = prompt.replace("\\\\", "\\") 
    prompt = prompt.replace("\\n", "\n") 
    prompt = prompt.replace("\\'", "'")    
    prompt = prompt.replace("\'", "'")    
    prompt = prompt.replace('\\"', '"')
    prompt = prompt.replace('\"', '"')
    prompt = prompt.replace('<END>', '') 

    return prompt

def get_completion(prompt, istext):
    """
    Get the completion from the LLM backend.

    Parameters:
    - prompt (str): The prompt to send to the LLM backend.
    - istext (str): Whether the prompt is text or not.

    Returns:
    - str: The generated completion
    """
    # Check if the prompt is text or not
    if istext == "True":
        prompt = build_prompt(prompt)

    # Set the header for the request
    headers = {
        "Content-Type": "application/json",
        "Authorization": f"Bearer {CONFIG['LLM']['api_key']}"
    }

    # Handle OpenAI backend
    if CONFIG['LLM']['llm_backend'] == "openai":
        url = f"{CONFIG['LLM']['base_url']}/v1/chat/completions"
        data = {
            "model": CONFIG['LLM']['openai_model'],  # GPT-4 or GPT-3.5-turbo
            "messages": [
                {"role": "system", "content": CONFIG['LLM']['systemprompt']},
                {"role": "user", "content": prompt}
            ],
            "max_tokens": CONFIG['LLM']['max_tokens'],
            "temperature": CONFIG['LLM']['temperature'],
            "top_p": CONFIG['LLM']['top_p']
        }
    # Handle Ooba backend
    elif CONFIG['LLM']['llm_backend'] == "ooba":
        url = f"{CONFIG['LLM']['base_url']}/v1/completions"
        data = {
            "prompt": prompt,
            "max_tokens": CONFIG['LLM']['max_tokens'],
            "temperature": CONFIG['LLM']['temperature'],
            "top_p": CONFIG['LLM']['top_p'],
            "seed": CONFIG['LLM']['seed']
        }
    # Handle Tabby backend
    elif CONFIG['LLM']['llm_backend'] == "tabby":
        url = f"{CONFIG['LLM']['base_url']}/v1/completions"
        data = {
            "prompt": prompt,
            "max_tokens": CONFIG['LLM']['max_tokens'],
            "temperature": CONFIG['LLM']['temperature'],
            "top_p": CONFIG['LLM']['top_p']
        }
    else:
        raise ValueError(f"Unsupported LLM backend: {CONFIG['LLM']['llm_backend']}")

    # Send the request and get the response
    response = requests.post(url, headers=headers, data=json.dumps(data))
    try:
        response.raise_for_status()  # Handle HTTP errors
    except requests.exceptions.RequestException as e:
        print(f"[{datetime.now().strftime('%Y-%m-%d %H:%M:%S')}] ERROR: LLM request failed: {e}")
        return None  # Return None for failed requests

    # Check if the response is successful
    if istext == "False":
        text_to_read = extract_text(response.json(), True)
    else:
        text_to_read = extract_text(response.json(), False)
    text_to_read = text_to_read.replace('<END>', '') # Without this if may continue on forever (max token)

    return(text_to_read)

def process_completion(text):
    """
    Process the user input and generate a response using the Large Language Model (LLM) backend.

    Parameters:
    - text (str): The user input text.

    Returns:
    - str: The AI-generated response.
    """
    # Use the executor directly without 'with' statement
    future = executor.submit(get_completion, text, "True")
    botres = future.result()
    reply = llm_process(text, botres)
    return reply

# === Callback Functions ===
def wake_word_callback(wake_response):
    """
    Play initial response when wake word is detected.

    Parameters:
    - wake_response (str): The response to the wake word.
    """
    generate_tts_audio(wake_response, CONFIG['TTS']['ttsoption'], CONFIG['TTS']['azure_api_key'], CONFIG['TTS']['azure_region'], CONFIG['TTS']['ttsurl'], CONFIG['TTS']['toggle_charvoice'], CONFIG['TTS']['tts_voice'])

def utterance_callback(message):
    """
    Process the recognized message from STTManager and stream audio response to speakers.

    Parameters:
    - message (str): The recognized message from the Speech-to-Text (STT) module.
    """
    try:
        # Parse the user message
        message_dict = json.loads(message)
        if not message_dict.get('text'):  # Handles cases where text is "" or missing
            #print(f"[{datetime.now().strftime('%Y-%m-%d %H:%M:%S')}] TARS: Going Idle...")
            return
        #Print the response
        print(f"[{datetime.now().strftime('%Y-%m-%d %H:%M:%S')}] USER: {message_dict['text']}")

        # Check for shutdown command
        if "shutdown pc" in message_dict['text'].lower():
            print(f"[{datetime.now().strftime('%Y-%m-%d %H:%M:%S')}] SHUTDOWN: Shutting down the PC...")
            os.system('shutdown /s /t 0')
            return  # Exit function after issuing shutdown command
        
        # Process the message using process_completion
        reply = process_completion(message_dict['text'])  # Process the message

        print(f"[{datetime.now().strftime('%Y-%m-%d %H:%M:%S')}] TARS: {reply}")
        # Stream TTS audio to speakers
        #print("Fetching TTS audio...")
        generate_tts_audio(reply, CONFIG['TTS']['ttsoption'], CONFIG['TTS']['azure_api_key'], CONFIG['TTS']['azure_region'], CONFIG['TTS']['ttsurl'], CONFIG['TTS']['toggle_charvoice'], CONFIG['TTS']['tts_voice'])

    except json.JSONDecodeError:
        print(f"[{datetime.now().strftime('%Y-%m-%d %H:%M:%S')}] ERROR: Invalid JSON format. Could not process user message.")
    except Exception as e:
        print(f"[{datetime.now().strftime('%Y-%m-%d %H:%M:%S')}] ERROR: {e}")

def post_utterance_callback():
    """
    Restart listening for another utterance after handling the current one.
    """
    global stt_manager
    stt_manager._transcribe_utterance()

# === Initialization ===
def initialize_managers(mem_manager, char_manager, stt_mgr):
    """
    Pass in the shared instances for MemoryManager, CharacterManager, and STTManager.
    
    Parameters:
    - mem_manager: The MemoryManager instance from app.py.
    - char_manager: The CharacterManager instance from app.py.
    - stt_mgr: The STTManager instance from app.py.
    """
    global memory_manager, character_manager, stt_manager
    memory_manager = mem_manager
    character_manager = char_manager
    stt_manager = stt_mgr

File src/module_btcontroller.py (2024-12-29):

"""
module_btcontroller.py

Provides functionality for managing and interpreting Bluetooth gamepad input 
to control servos and execute specific actions in the TARS-AI system.

This module listens to gamepad events such as button presses, joystick movements, 
and D-pad directions, mapping these events to corresponding robotic movements or 
in-app commands. 
"""

import evdev
import time
from datetime import datetime
from module_servoctl import *
from evdev import InputDevice, categorize, ecodes, list_devices
import Adafruit_PCA9685

global posevar

try:
    pwm = Adafruit_PCA9685.PCA9685(busnum=1)  # Specify I2C bus 1
    pwm.set_pwm_freq(60)  # Set frequency to 60 Hz
except FileNotFoundError as e:
    print(f"[{datetime.now().strftime('%Y-%m-%d %H:%M:%S')}] ERROR: I2C device not found. Ensure that /dev/i2c-1 exists. Details: {e}")
    pwm = None  # Fallback if hardware is unavailable
except Exception as e:
    print(f"[{datetime.now().strftime('%Y-%m-%d %H:%M:%S')}] ERROR: Unexpected error during PCA9685 initialization: {e}")
    pwm = None  # Fallback if hardware is unavailable



# Set initial servo positions
if pwm:
    try:
        # Port
        pwm.set_pwm(3, 3, 610)
        pwm.set_pwm(4, 4, 570)
        pwm.set_pwm(5, 5, 570)
        # Starboard
        pwm.set_pwm(6, 6, 200)
        pwm.set_pwm(7, 7, 200)
        pwm.set_pwm(8, 8, 240)
    except Exception as e:
        print(f"Error setting initial servo positions: {e}")

lTrg = 37
rTrg = 50
upBtn = 46
downBtn = 32
lBtn = 18
rBtn = 33
xBtn = 23
yBtn = 35
aBtn = 36
bBtn = 34
minusBtn = 49
plusBtn = 24

global gamepad_path
toggle = True
posevar = False

SECRET_CODE = [
    "up", "up", "down", "down", "left", "right", "left", "right", "B", "A Button", "Start Button"
]

# Track user input
input_sequence = []

def find_controller(controller_name):
    global gamepad_path
    """
    Search for a controller by its name.
    """
    devices = [InputDevice(path) for path in list_devices()]
    for device in devices:
        if controller_name.lower() in device.name.lower():
            print(f"[{datetime.now().strftime('%Y-%m-%d %H:%M:%S')}] LOAD: Controller found: {device.name} at {device.path}")
            gamepad_path = device.path
            return device
    print(f"[{datetime.now().strftime('%Y-%m-%d %H:%M:%S')}] LOAD: {controller_name} Not found, Searching...")
    return None

def check_secret_code(button_name):
    global input_sequence
    input_sequence.append(button_name)

    # Check if the current sequence matches the start of the secret code
    if input_sequence == SECRET_CODE[:len(input_sequence)]:
        # If the sequence matches the full secret code
        if len(input_sequence) == len(SECRET_CODE):
            from module_secrets import play_video_fullscreen
            play_video_fullscreen("secrets/secret.mp4", rotation_angle=90)
            input_sequence = []  # Reset the sequence after the code is entered
    else:
        # If the sequence doesn't match, reset it
        #print(f"Invalid sequence detected: {input_sequence}. Resetting...")
        input_sequence = []

#functions to move
def stepForward():
	height_neutral_to_up()
	torso_neutral_to_forwards()
	torso_bump()
	torso_return()

def turnRight():
	neutral_to_down()
	turn_right()
	down_to_neutral()
	neutral_from_right()

def turnLeft():
	neutral_to_down()
	turn_left()
	down_to_neutral()
	neutral_from_left()

def poseaction():
    neutral_to_down()
    torso_neutral_to_backwards()
    down_to_up()

def unposeaction():
    torso_return2()  
        
        
# D-Pad Actions (pressed and released)
def action_dpad_up_pressed():
    #print(f"[{datetime.now().strftime('%Y-%m-%d %H:%M:%S')}] CTRL: D-Pad Up pressed! Let's move up!")
    stepForward()

def action_dpad_down_pressed():
    print(f"[{datetime.now().strftime('%Y-%m-%d %H:%M:%S')}] CTRL: D-Pad Down pressed! Let's move down!")
    global posevar
    
    if posevar == False:
        poseaction()
        posevar = True
    elif posevar == True:
        unposeaction()
        posevar = False

def action_dpad_left_pressed():
    #print(f"[{datetime.now().strftime('%Y-%m-%d %H:%M:%S')}] CTRL: D-Pad Left pressed! Moving left!")
    turnLeft()

def action_dpad_right_pressed():
    #print(f"[{datetime.now().strftime('%Y-%m-%d %H:%M:%S')}] CTRL: D-Pad Right pressed! Moving right!")
    turnRight()

def action_dpad_up_released():
    #print(f"[{datetime.now().strftime('%Y-%m-%d %H:%M:%S')}] CTRL: D-Pad Up released! Stopping move up.")
    pass

def action_dpad_down_released():
    #print(f"[{datetime.now().strftime('%Y-%m-%d %H:%M:%S')}] CTRL: D-Pad Down released! Stopping move down.")
    pass

def action_dpad_left_released():
    #print(f"[{datetime.now().strftime('%Y-%m-%d %H:%M:%S')}] CTRL: D-Pad Left released! Stopping move left.")
    pass

def action_dpad_right_released():
    #print(f"[{datetime.now().strftime('%Y-%m-%d %H:%M:%S')}] CTRL: D-Pad Right released! Stopping move right.")
    pass

# Joystick Actions (show values when moved)
def action_left_stick_move(x_value, y_value):
    #print(f"[{datetime.now().strftime('%Y-%m-%d %H:%M:%S')}] CTRL: Left Stick moved to X: {x_value}, Y: {y_value}")
    pass

def action_right_stick_move(x_value, y_value):
    #print(f"[{datetime.now().strftime('%Y-%m-%d %H:%M:%S')}] CTRL: Right Stick moved to X: {x_value}, Y: {y_value}")
    pass

# Define custom actions for specific buttons (pressed)
def action_a_button_pressed():
    #print(f"[{datetime.now().strftime('%Y-%m-%d %H:%M:%S')}] CTRL: A Button? Are you trying to jump?")
    global toggle
    if toggle == True:
        starHandPlus()
    elif toggle == False:
        starHandMinus()

def action_b_button_pressed():
    #print(f"[{datetime.now().strftime('%Y-%m-%d %H:%M:%S')}] CTRL: Oh no, the B! Self-destruct initiated... just kidding!")
    global toggle
    if toggle == True:
        portHandPlus()
    elif toggle == False:
        portHandMinus()

def action_x_button_pressed():
    #print(f"[{datetime.now().strftime('%Y-%m-%d %H:%M:%S')}] CTRL: Hey, stop pushing my X Button!")
    global toggle
    if toggle == True:
        starForarmPlus()
    elif toggle == False:
        starForarmMinus()

def action_y_button_pressed():
    #print(f"[{datetime.now().strftime('%Y-%m-%d %H:%M:%S')}] CTRL: Y Button? I hope you know what youre doing!")
    global toggle
    if toggle == True:
        portForarmPlus()
    elif toggle == False:
        portForarmMinus()

def action_r1_button_pressed():
    #print(f"[{datetime.now().strftime('%Y-%m-%d %H:%M:%S')}] CTRL: R1 Button pressed! Thats the turbo button!")
    global toggle
    if toggle == True:
        starMainPlus()
    elif toggle == False:
        starMainMinus()

def action_l1_button_pressed():
    #print(f"[{datetime.now().strftime('%Y-%m-%d %H:%M:%S')}] CTRL: L1 Button activated! Shields up!")
    global toggle
    if toggle == True:
        portMainPlus()
    elif toggle == False:
        portMainMinus()
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

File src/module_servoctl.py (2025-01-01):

"""
module_servoctl.py

Servo Control Module for TARS-AI Application.

This module provides a comprehensive set of functions to control servos in TARS, enabling complex movements such as:
- Torso height adjustment.
- Torso rotation to forward/backward positions.
- Controlled arm and hand movements.
- Synchronized servo adjustments for smooth motion transitions.
"""

from __future__ import division
import time
import Adafruit_PCA9685
from threading import Thread
from datetime import datetime

from module_config import load_config
config = load_config()


try:
    # Attempt to initialize the PCA9685 using I2C
    pwm = Adafruit_PCA9685.PCA9685(busnum=1)
    pwm.set_pwm_freq(60)  # Set frequency to 60 Hz for servos
except FileNotFoundError as e:
    print(f"[{datetime.now().strftime('%Y-%m-%d %H:%M:%S')}] ERROR: I2C device not found. Ensure that /dev/i2c-1 exists. Details: {e}")
    pwm = None  # Fallback if hardware is unavailable
except Exception as e:
    print(f"[{datetime.now().strftime('%Y-%m-%d %H:%M:%S')}] ERROR: Unexpected error during PCA9685 initialization: {e}")
    pwm = None  # Fallback if hardware is unavailable

# Servo Configuration Mapping with Integer Casting
portMain = int(config["SERVO"]["portMain"])
starMain = int(config["SERVO"]["starMain"])
portForarm = int(config["SERVO"]["portForarm"])
starForarm = int(config["SERVO"]["starForarm"])
portHand = int(config["SERVO"]["portHand"])
starHand = int(config["SERVO"]["starHand"])

# Center Lift Servo (0) Values
upHeight = int(config["SERVO"]["upHeight"])
neutralHeight = int(config["SERVO"]["neutralHeight"])
downHeight = int(config["SERVO"]["downHeight"])

# Port Drive Servo (1) Values
forwardPort = int(config["SERVO"]["forwardPort"])
neutralPort = int(config["SERVO"]["neutralPort"])
backPort = int(config["SERVO"]["backPort"])
perfectportoffset = int(config["SERVO"]["perfectportoffset"])  # Use this to fine-tune if it's off by a few degrees

# Starboard Drive Servo (2) Values
forwardStarboard = int(config["SERVO"]["forwardStarboard"])
neutralStarboard = int(config["SERVO"]["neutralStarboard"])
backStarboard = int(config["SERVO"]["backStarboard"])
perfectStaroffset = int(config["SERVO"]["perfectStaroffset"])  # Use this to fine-tune if it's off by a few degrees


# moves the torso from a neutral position upwards, allowing the torso to pivot forwards or backwards
def height_neutral_to_up():
	height = neutralHeight
	print('setting center servo (0) Neutral --> Up position')
	while (height > upHeight):
		height = height - 1
		pwm.set_pwm(0, 0, height)
		time.sleep(0.001)
	print('center servo (0) set to: Up position\n ')

# rotates the torso outwards, enough so that when TARS pivots and lands, the bottom of the torso is 
# flush with the ground. Making the torso flush with the ground is an intentional improvement from
# previous programs, where TARS would land and then slide a little on smooth surfaces, which while
# allowing for a simple walking program, inhibited TARS' ability to walk on surfaces with different 
# coefficients of friction
def torso_neutral_to_forwards():
	port = neutralPort
	starboard = neutralStarboard
	print('setting port and starboard servos (1)(2) Neutral --> Forward')
	while (port < forwardPort):
		port = port + 1
		starboard = starboard - 1
		pwm.set_pwm(1, 1, port)
		pwm.set_pwm(2, 2, starboard)
		time.sleep(0.0001)
	print('port and starboard servos (1)(2) set to: Forward position\n ')

def torso_neutral_to_backwards():
	port = neutralPort
	starboard = neutralStarboard
	print('setting port and starboard servos (1)(2) Neutral --> Forward')
	while (port > backPort):
		port = port - 1
		starboard = starboard + 1
		pwm.set_pwm(1, 1, port)
		pwm.set_pwm(2, 2, starboard)
		time.sleep(0.0001)
	print('port and starboard servos (1)(2) set to: Forward position\n ')

# rapidly shifts the torso height from UP --> DOWN and then returns --> UP, which should cause TARS 
# to pivot and land on it's torso
def torso_bump():
	height = upHeight
	print('performing a torso bump\nsetting center servo (0) Up --> Down position FAST')
	while (height < downHeight):
		height = height + 2
		pwm.set_pwm(0, 0, height)
		time.sleep(0.000001)
	print('setting center servo (0) Down --> Up position FAST')
	while (height > upHeight):
		height = height - 1
		pwm.set_pwm(0, 0, height)
		time.sleep(0.0001)
	print('center servo (0) returned to Up position\n')
	
# returns the torso's vertical height and rotation to centered values from up height and forward 
# rotation. Activates two external functions so movement in both axes can occur in parallel.
def torso_return():
	t1 = Thread(target = torso_return_rotation)
	t2 = Thread(target = torso_return_vertical)
	
	t1.start()
	t2.start()

# returns torso's rotation to neutral from forward
def torso_return_rotation():
	port = forwardPort
	starboard = forwardStarboard
	print('setting port and starboard servos (1)(2) Forward --> Neutral position')
	while (port > neutralPort):
		port = port - 1
		starboard = starboard + 1
		pwm.set_pwm(1, 1, port)
		pwm.set_pwm(2, 2, starboard)
		time.sleep(0.005)
	print('port and starboard servos (1)(2) set to: Neutral position\n ')

# returns torso's vertical to neutral from up	
def torso_return_vertical():
	height = upHeight
	print('setting center servo (0) Up --> Down position')
	# moving the torso down to create clearance for the rotation of the legs
	while (height < downHeight):
		height = height + 1
		pwm.set_pwm(0, 0, height)
		time.sleep(0.00005)
	# moving the torso up from down to neutral
	#time.sleep(.2)
	while (height > neutralHeight):
		height = height - 1
		pwm.set_pwm(0, 0, height)
		time.sleep(0.00001)
	print('center servo (0) set to: Neutral position\n ')

def torso_return2():
	t1 = Thread(target = torso_return_rotation2)
	t2 = Thread(target = torso_return_vertical2)
	
	t1.start()
	t2.start()

# returns torso's rotation to neutral from forward
def torso_return_rotation2():
	port = backPort
	starboard = backStarboard
	print('setting port and starboard servos (1)(2) Forward --> Neutral position')
	while (port < neutralPort):
		port = port + 1
		starboard = starboard - 1
		pwm.set_pwm(1, 1, port)
		pwm.set_pwm(2, 2, starboard)
		time.sleep(0.01)
	print('port and starboard servos (1)(2) set to: Neutral position\n ')

# returns torso's vertical to neutral from up	
def torso_return_vertical2():
	height = upHeight
	print('setting center servo (0) Up --> Down position')
	# moving the torso down to create clearance for the rotation of the legs
	while (height < downHeight):
		height = height + 1
		pwm.set_pwm(0, 0, height)
		time.sleep(0.001)
	# moving the torso up from down to neutral
	time.sleep(.25)
	while (height > neutralHeight):
		height = height - 1
		pwm.set_pwm(0, 0, height)
		time.sleep(0.001)
	print('center servo (0) set to: Neutral position\n ')
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

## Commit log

2024-12-26 new file: .DS_Store modified: .gitignore new file: 3d Printer Files/Arm Chasis Lid x2.stl new file: 3d Printer Files/Arm Left (Top Chassis).stl new file: 3d Printer Files/Arm Left 1 Finger.stl new fi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
    [12 ch pwm.stl, 525125.STEP, Arm Chasis Lid x2.stl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]
2024-12-26 modified: Brain/app-servotester.py
2024-12-27 new file: 3d Printer Files/Chassis Upper Lid (v9) Speaker and Cam Mod.stl new file: Brain/config - example.ini
    [Chassis Upper Lid (v9) Speaker and Cam Mod.stl]
2024-12-27 new file: 3d Printer Files/Chassis Lower Lid MOD PCT (mirror) makes space for GPIO.stl
    [Chassis Lower Lid MOD PCT (mirror) makes space for GPIO.stl]
2024-12-27 renamed: 3d Printer Files/Other/Lower Lid (v9) PCT MOD.stl -> 3d Printer Files/Chassis Lower Lid MOD PCT.stl
    [Chassis Lower Lid MOD PCT.stl]
2024-12-28 RELEASE v1.0: Hello World, Hello TARS!
    [training_data.csv]
2024-12-28 Update ENVSETUP.md with additional Azure TTS instructions. Fixed module_stt mic_index bug.
    [module_stt.py]
2024-12-29 Fixed character loading bug
    [module_character.py, module_config.py, module_main.py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]
2024-12-30 Fixed oversight in path for piper tts
    [module_piper.py]
2024-12-30 Various bug fixes and updates
    [training_data.csv]
2024-12-30 minor fix to stt url
    [module_stt.py]
2024-12-30 updates to app-server to supress new errors, redirect to vision cache local also
    [app-server.py]
2024-12-30 Update to config for perm storage of servo veriables
2024-12-31 misc fixes and mods: flexors, lids, display support
    [5in display spacer.stl, Arm Right Long Finger Lid countersunk.stl, Chassis Upper Lid v9 5in narrow.stl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]
2025-01-01 added M3 grub screws
